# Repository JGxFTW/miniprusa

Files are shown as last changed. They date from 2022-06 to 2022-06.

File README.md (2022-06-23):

# miniprusa MC3 
## FDM/FFF 3D printer project

Heavy Duty, small factor, cartesian (bedslinger) machine capable of printing high detail plastic prints (PLA, PETG, TPU and possibly ABS, ASA, other high-temp materials). Project is loosely based on Bearmod project for Prusa i3. Utilizes out-of-the-shelf components and 3d prints.

Fusion360 model: https://a360.co/3Ne5RhL

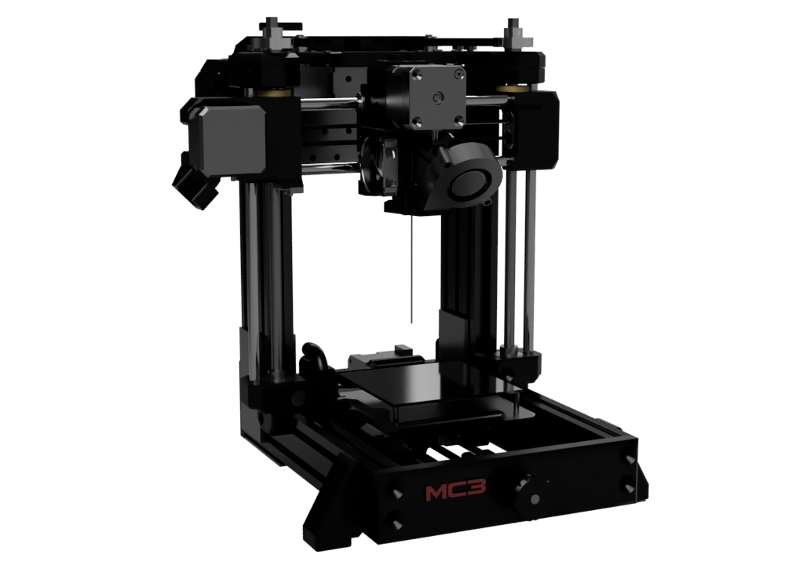
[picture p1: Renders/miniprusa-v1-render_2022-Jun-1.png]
miniprusa render


## Features

- ~100x100x110 [mm] build volume
- Direct MK3s extruder [remixed] for MK8/HobbGoblin drive gear and filament sensor (switch)
- Popular [Bearmod] XZ axis design, inverted
- LM8UU and 8mm smooth rods linear guide
- Rigid metal frame out of steel plates, 2040 and 2060 aluminum profiles
- Dual Z axis is driven independent with 1:2 gear ratio with nema 17 motor for each side
- [Marlin] 2.0.9.1 with auto bed leveling
- Custom ergonomic controller with OLED and encoder

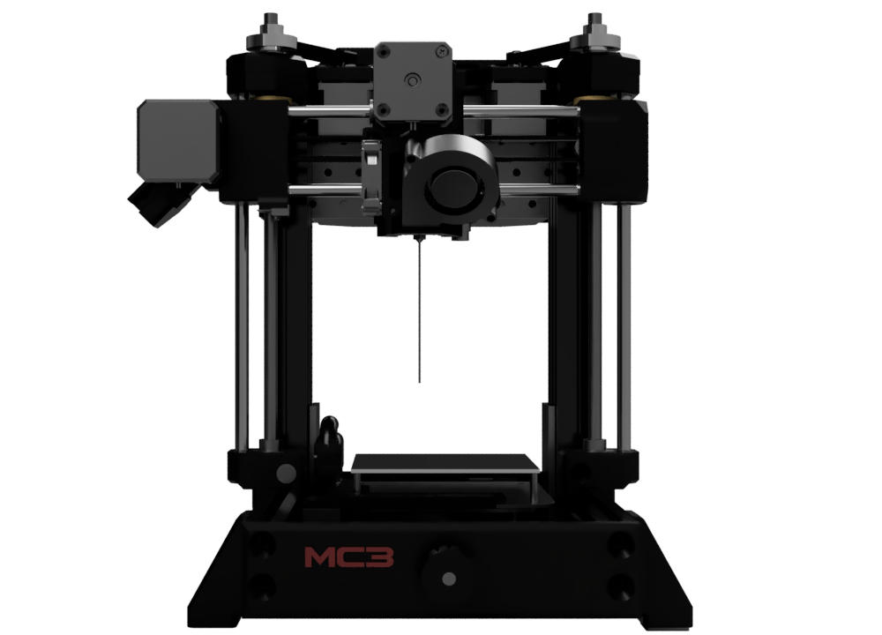
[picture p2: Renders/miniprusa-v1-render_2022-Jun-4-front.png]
miniprusa render

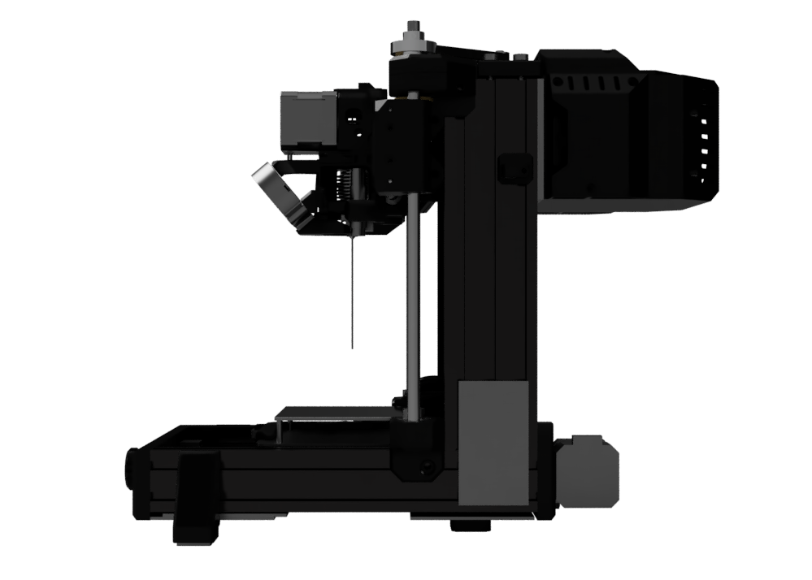
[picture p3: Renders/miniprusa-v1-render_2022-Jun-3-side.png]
miniprusa render

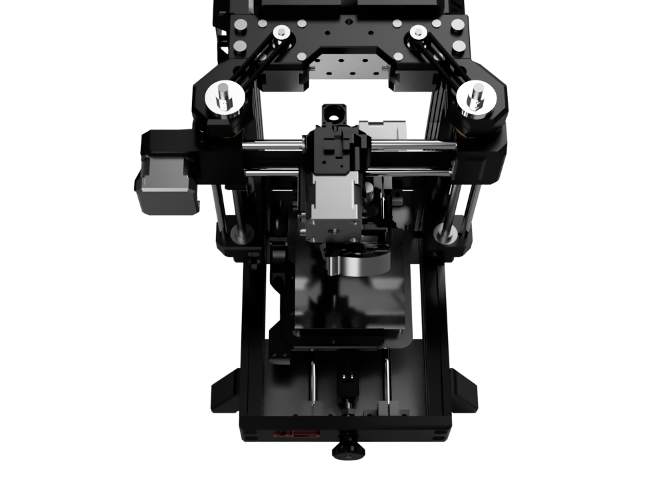
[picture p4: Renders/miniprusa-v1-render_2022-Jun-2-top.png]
miniprusa render

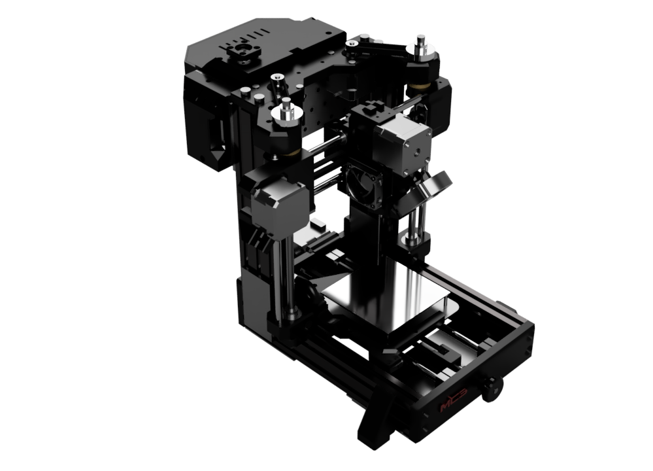
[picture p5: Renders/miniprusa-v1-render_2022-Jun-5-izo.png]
miniprusa render


## Technical details

### Frame
Frame consists of 2040 and 2060 aluminum extrusion profiles with 6mm groove. Steel plates and 3 printed bars (front, back and top) are holding extrusions in place secured with M5 screws and t-nuts.

### XYZ drive
Nema 17 stepper drivers for all axes. GT2 belt and pulleys. Dual Z axis consist of two trapezoidal screws with 8mm pitch (TR8x2) driven by independent motors with 1:2 gear ratio (GT2 T20 and GT2 T40).

### Extruder
Extruder is simplified PRUSA MK3 extruder with HobbGoblin/MK8 drive gear and 624ZZ idler bearing (PRUSA MK2s style).

Very consistent extrusion ;) 

### Electronics
Currently project uses RAMPS (https://reprap.org/wiki/RAMPS_1.4), as it is the most common mainboard.

Link to: [OLED Controller with encoder] project.

Power supply should be at least 200W
PSU is not mounted on the frame as printer was supposed to be in enclosure.

### Additions
Two types of cable tubing hoses 10mm (X,Y axes and OLED controller) and 16/17mm (extruder)

## BOM
The design require printed parts, so owning, renting 3d printer or outsourcing is needed.
Material PETG (open) or ABS, ASA (especially, if enclosing) are recommended.

Full [BOM spreadsheet] file.

Summary:
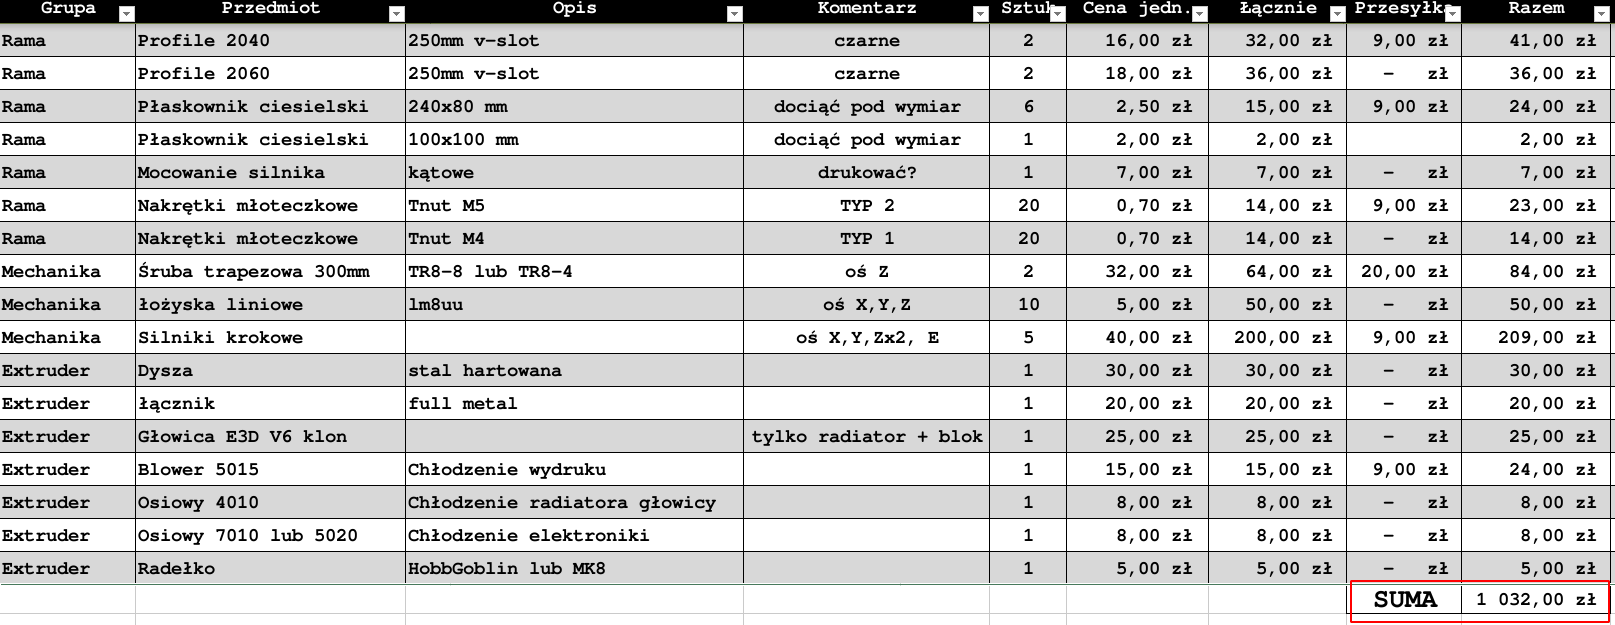
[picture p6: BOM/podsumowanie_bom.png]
BOM podsumowanie


## Firmware changes

Marlin 2.0.9.1 (v1.1) binary included - compiled for Ramps 1.4 and [miniOLED].

## Development

Want to contribute? Great!

To do:
> - revise Y axis
  - change endstop position
  - redesign bed plate
  - consider 
- redesign Z axis (one motor & synchronous belt drive)
> - BOM (translate, ensure correct number of screws and bolts, update links, double-check content)
 
Feel free to leave additional feedback.

[Forum thread] in Polish

## License

GPLv3

**Open Source, Hell Yeah!**

[//]: # (REFLINKS)
   [bearmod]: <https://www.thingiverse.com/thing:4362586>
   [remixed]: <https://www.thingiverse.com/thing:4566108>
   [Marlin]: <https://marlinfw.org/>
   [BOM spreadsheet]: <https://github.com/jgxftw/miniprusa/BOM/>
   [Reprap Forum thread]:<https://reprap.org/forum/read.php?13,499572,page=1>
   [Forum thread]: <https://reprapy.pl/viewtopic.php?f=78&t=7788&hilit=ma%C5%82a+czarna#p127598>
   [OLED Controller with encoder]: <https://github.com/jgxftw/minioled>
   [miniOLED]: <https://github.com/jgxftw/minioled>

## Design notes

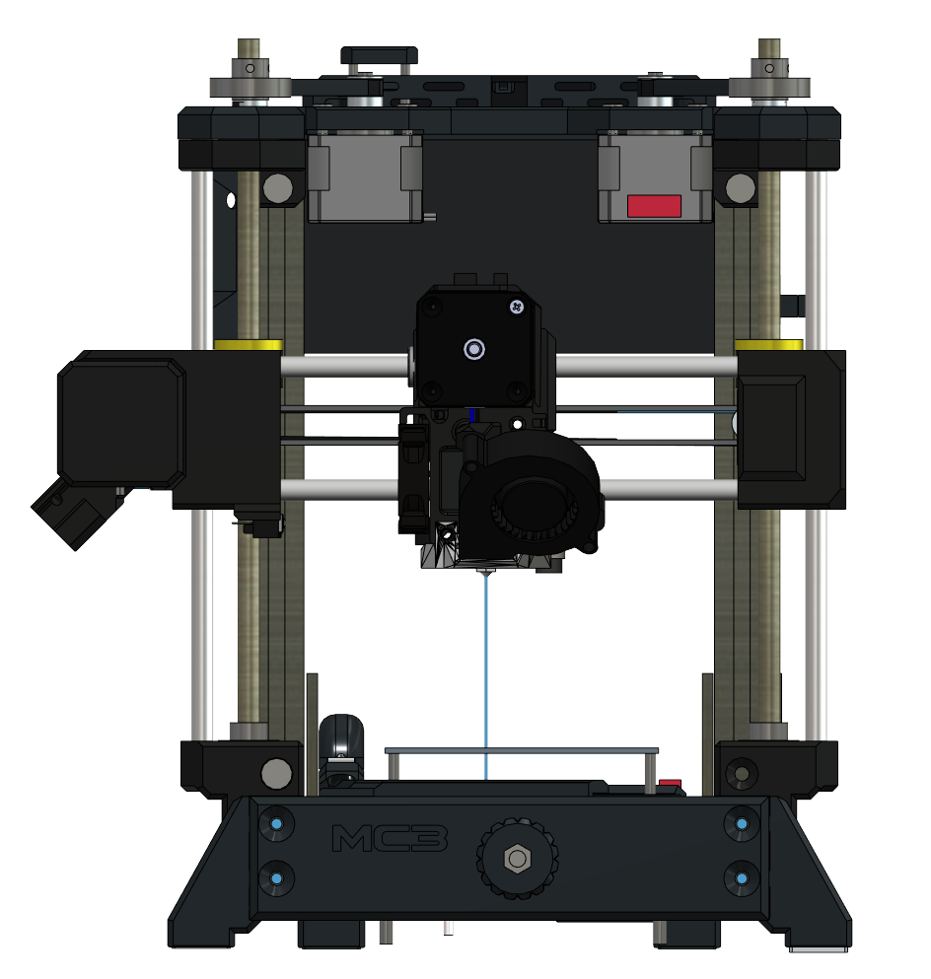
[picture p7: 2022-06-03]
Renders/miniprusa-all-v1-front.png

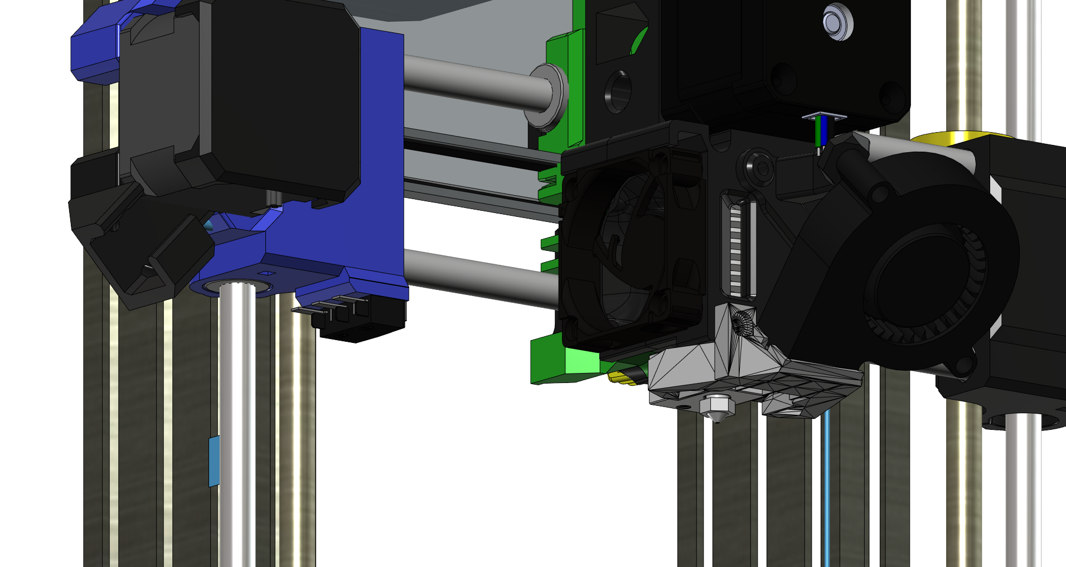
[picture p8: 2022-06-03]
Renders/endstop.png

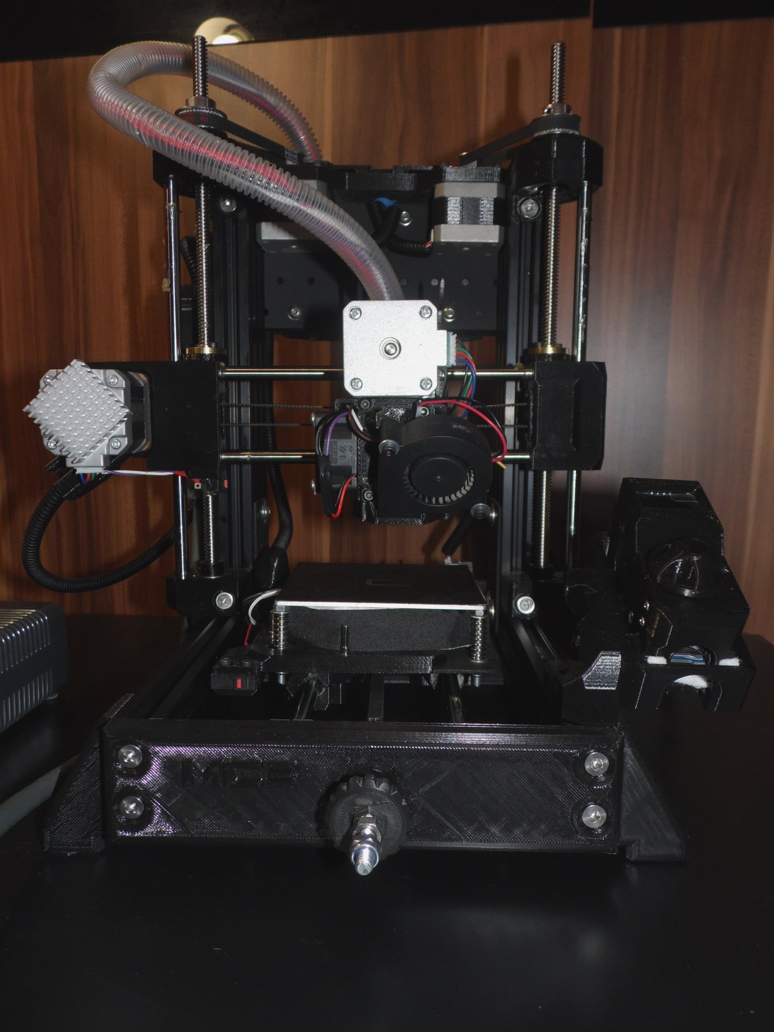
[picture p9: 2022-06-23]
Pictures/1-front3.JPG

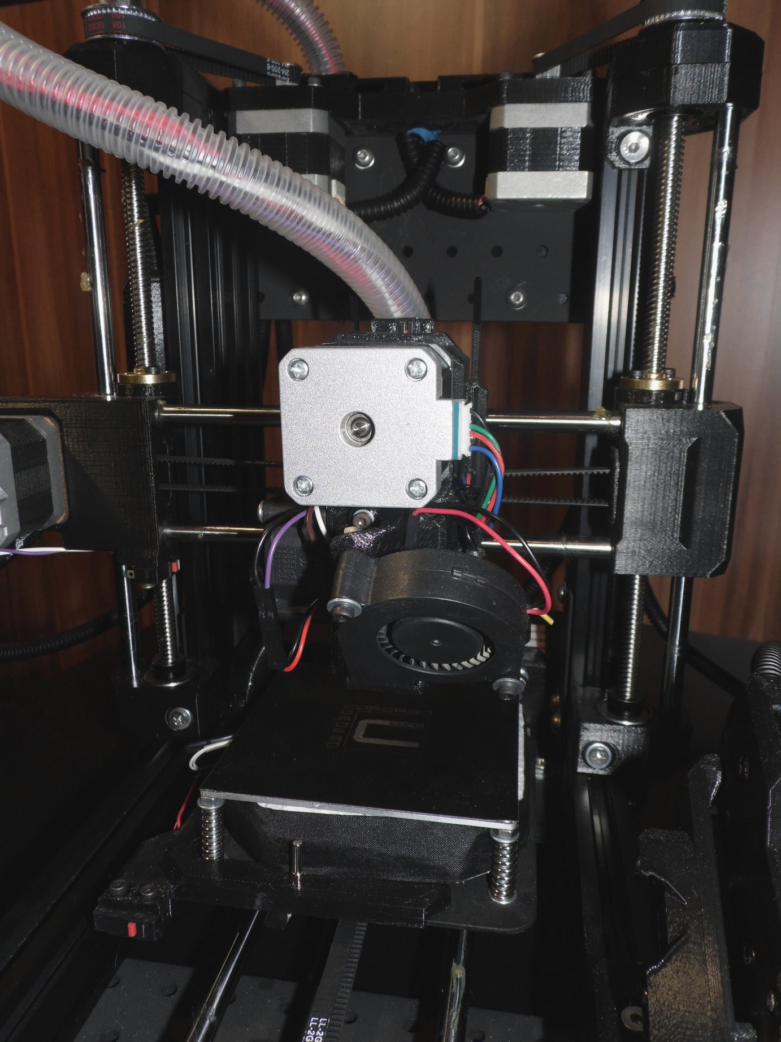
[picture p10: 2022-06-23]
Pictures/1-front2.JPG

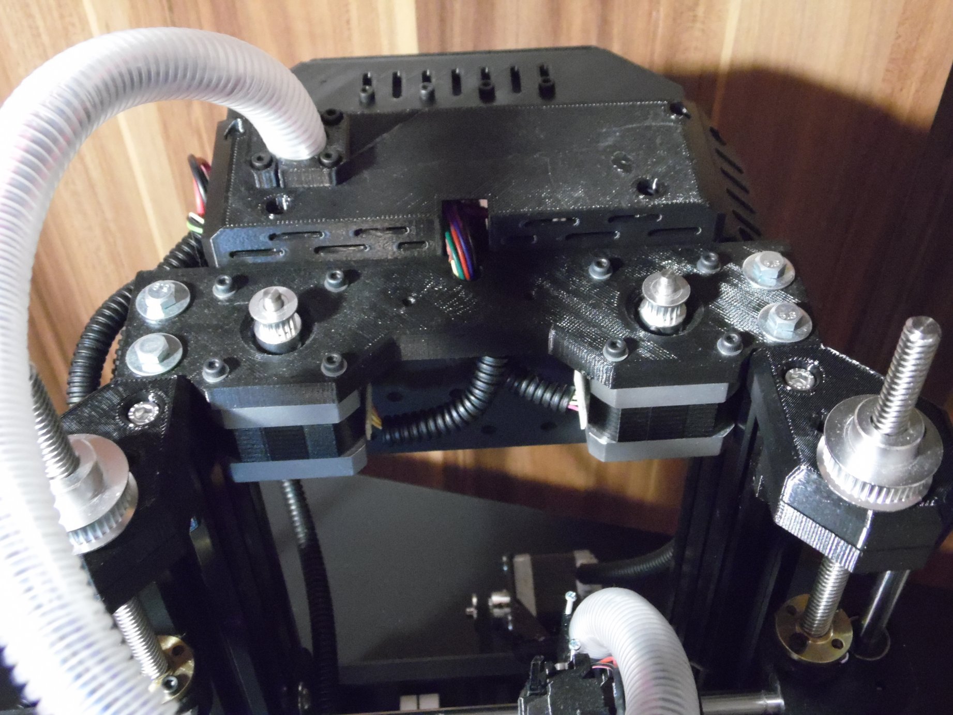
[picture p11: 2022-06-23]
Pictures/gora.JPG

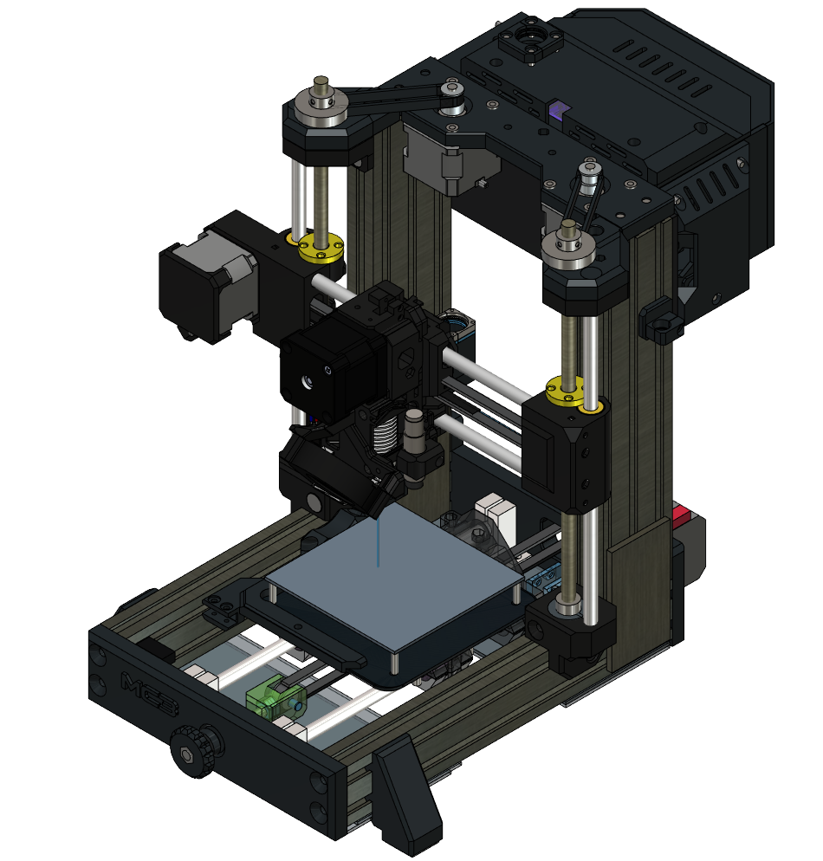
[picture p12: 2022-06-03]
Renders/miniprusa-all-v1-izo.png

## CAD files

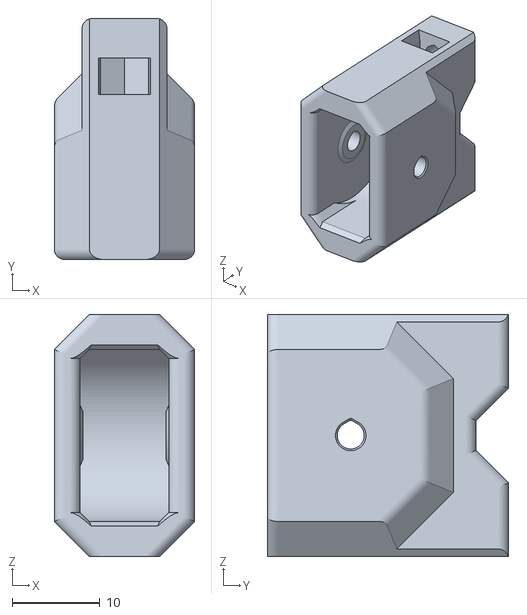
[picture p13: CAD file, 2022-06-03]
STL/Extruder/x-axis-idler-housing.stl
16.0 x 27.5 x 27.6

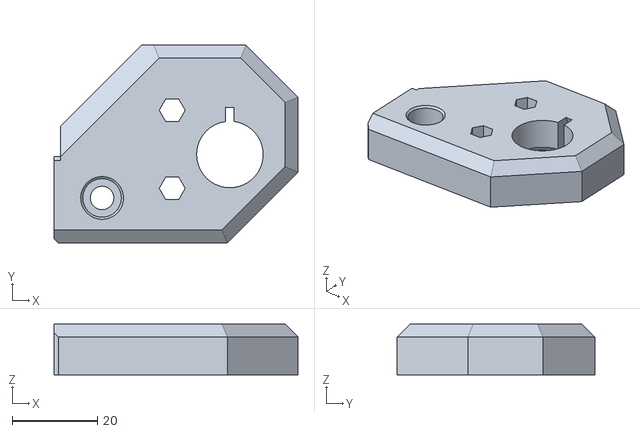
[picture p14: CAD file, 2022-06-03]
STL/z-axis-upper-cover-right.stl
57.1 x 46.2 x 11.9

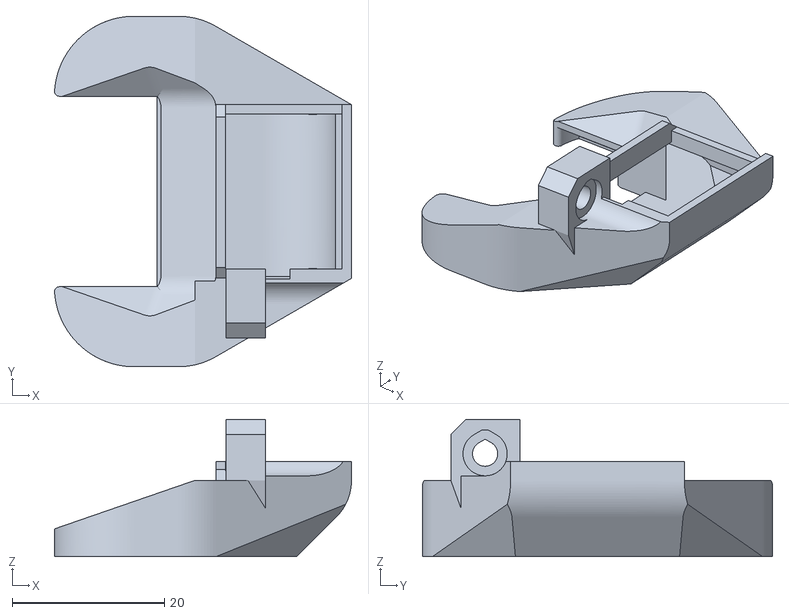
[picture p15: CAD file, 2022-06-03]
STL/Extruder/fan_duct_mk3_bearmod.stl
39.0 x 46.0 x 18.0

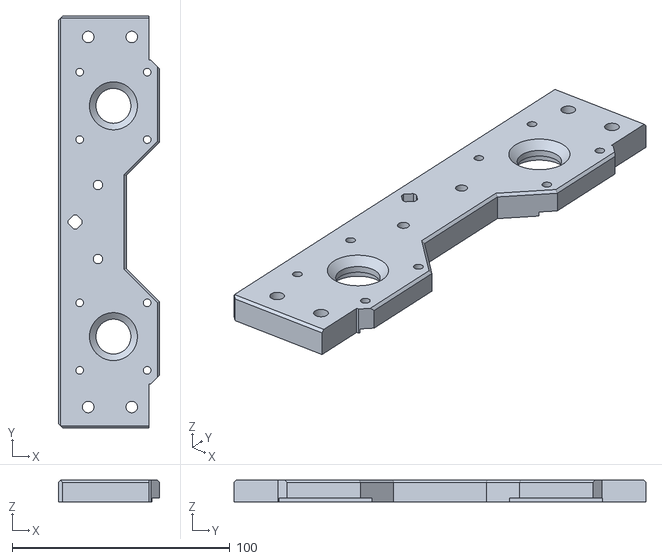
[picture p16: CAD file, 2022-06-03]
STL/z-axis-upper-reinforcementv_0_9.stl
46.6 x 189.2 x 10.0

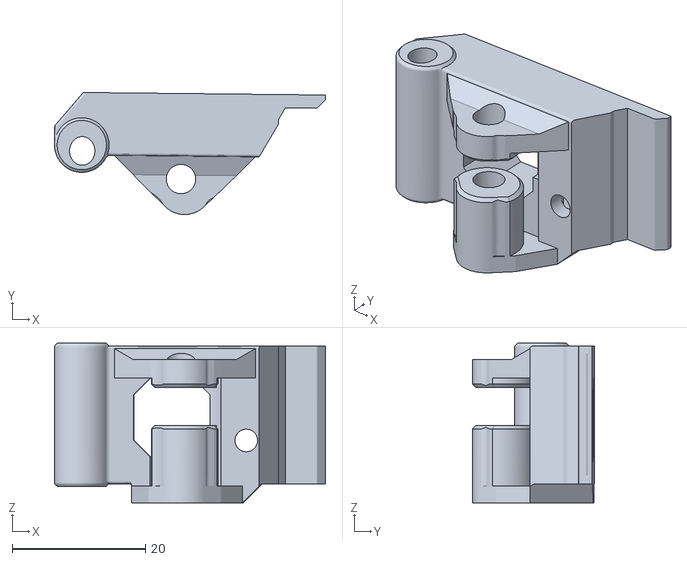
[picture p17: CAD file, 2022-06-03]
STL/Extruder/idler_v2.stl
40.7 x 18.3 x 23.9

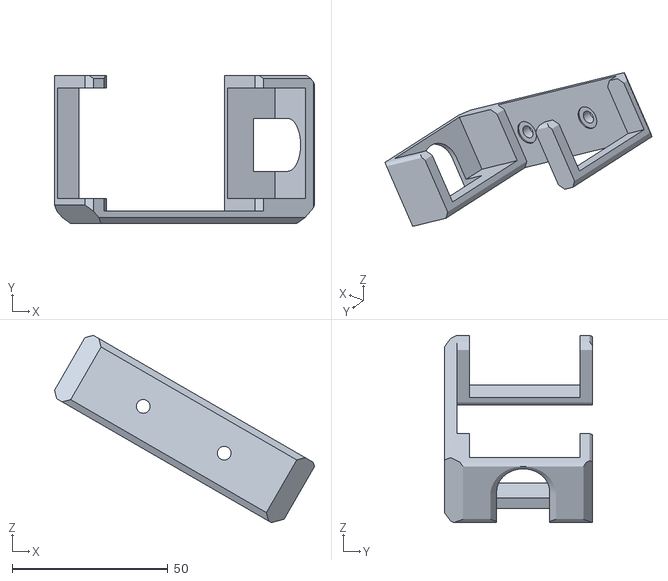
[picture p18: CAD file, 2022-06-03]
STL/lcd-screen-frame-mount-base.stl
83.4 x 47.6 x 60.1

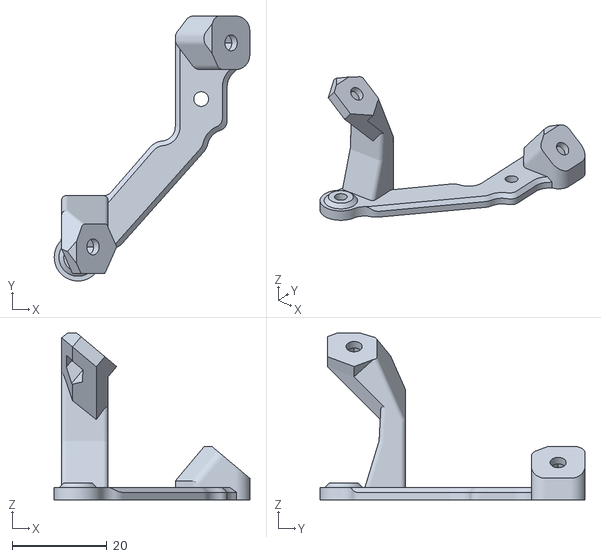
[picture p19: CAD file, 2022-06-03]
STL/Extruder/MK3_Extruder_fan_mount.stl
41.2 x 55.8 x 35.2

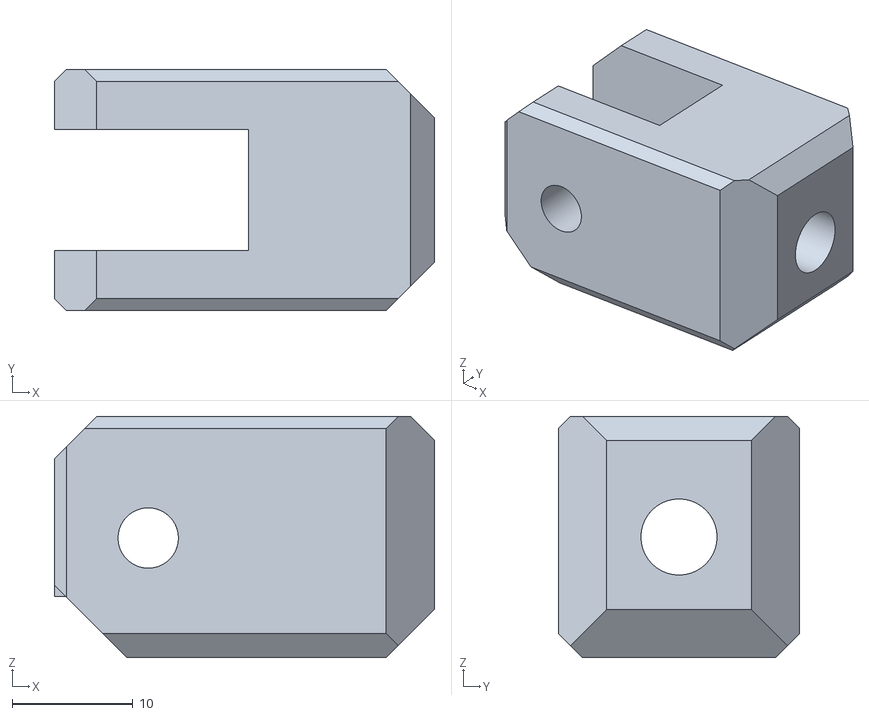
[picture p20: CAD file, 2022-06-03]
STL/y-axis-belt-tensioner-v3.stl
31.5 x 20.0 x 20.0

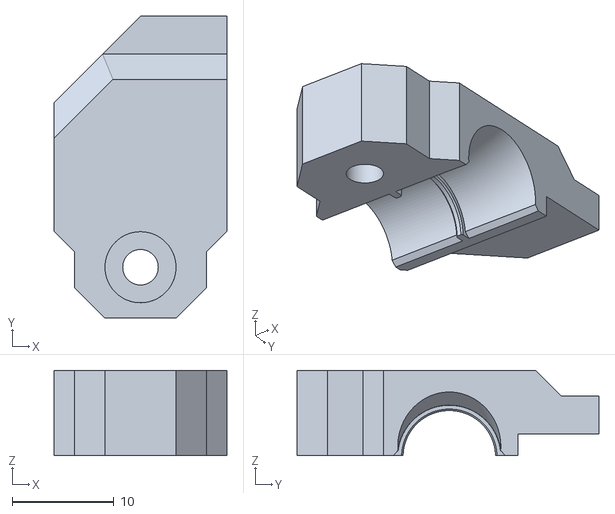
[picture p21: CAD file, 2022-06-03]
STL/bed-cable-chain-mount-clamp.stl
17.0 x 29.7 x 8.38

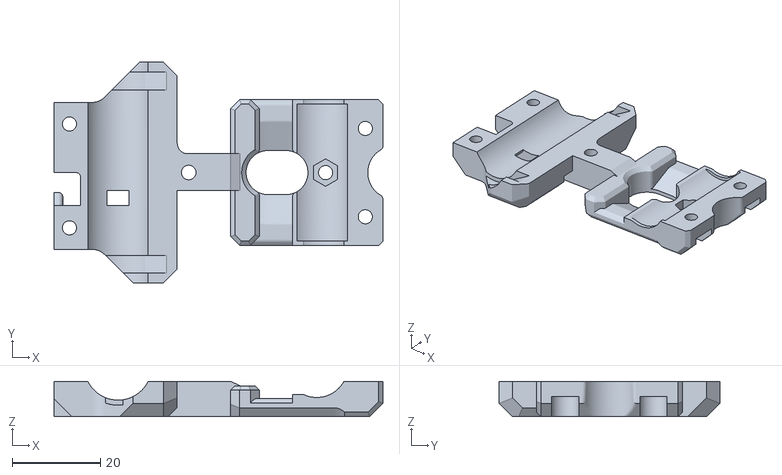
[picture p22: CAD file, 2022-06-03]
STL/Extruder/MK3_Extruder_x_carriage_cover.stl
74.5 x 50.0 x 8.00

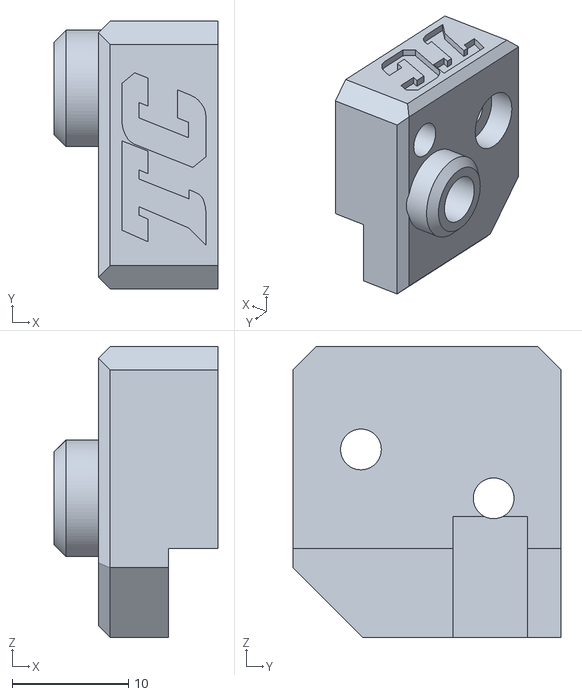
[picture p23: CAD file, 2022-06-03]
STL/Extruder/MK3_Extruder_rewizja_filament_sensor_cover.stl
14.1 x 23.0 x 25.0

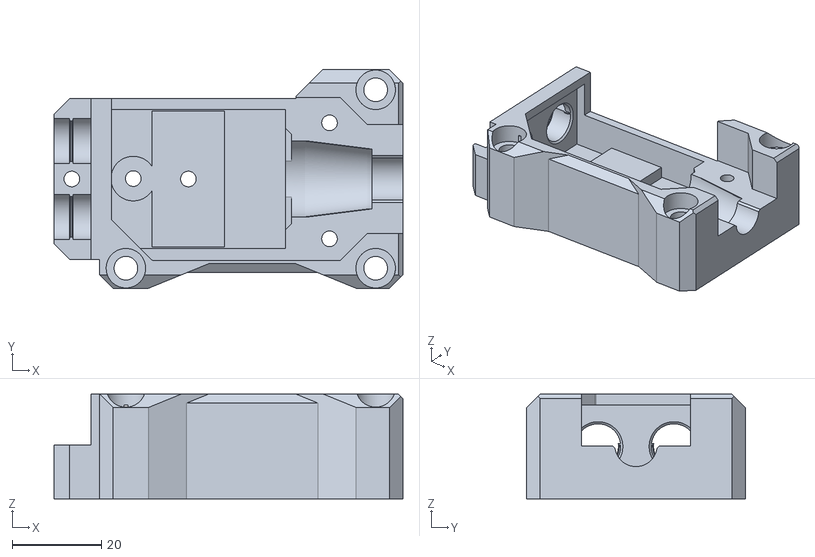
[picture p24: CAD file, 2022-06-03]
STL/xbox360-psu-power-inlet-base.stl
78.2 x 49.0 x 23.5

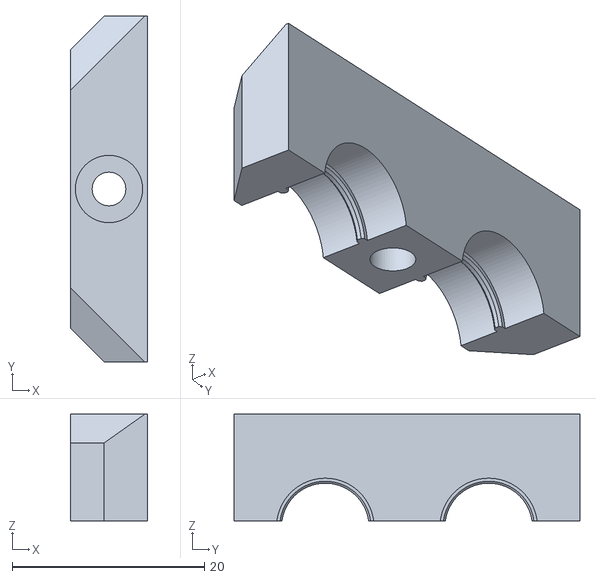
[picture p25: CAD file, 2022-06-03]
STL/xbox360-psu-power-inlet-clamp.stl
8.00 x 36.0 x 11.1

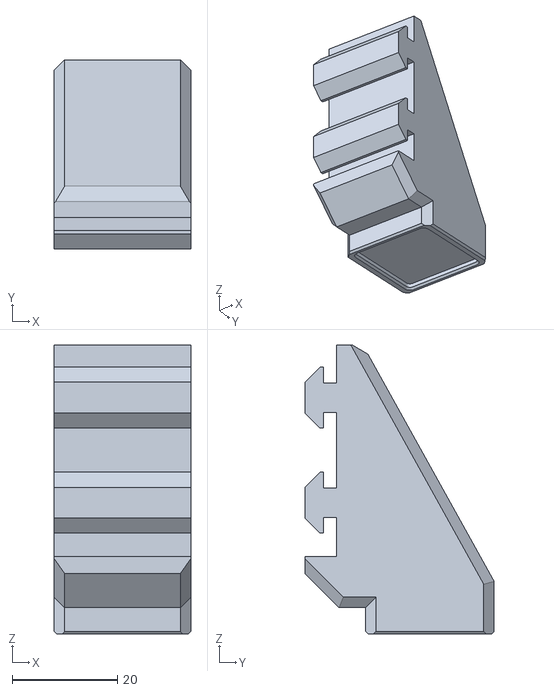
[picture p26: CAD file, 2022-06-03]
STL/base-legs.stl
26.0 x 36.1 x 55.0

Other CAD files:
STL/Extruder/MK3_Extruder_rewizja_idler.stl
STL/electronics-box-upper-cover-addon.stl
STL/z-axis-lower-trapezoidal-mount.stl
STL/LCD-screen-cable-mount.stl
STL/base-legs-v2.stl
STL/base-rear-legs.stl
STL/bed-cable-chain-mount-clamp-v2.stl
STL/bed-cable-chain-mount-clamp-v3.stl
STL/bed-cable-chain-mount-clamp-v4.stl
STL/bed-cable-chain-mount-clamp-v5stl.stl
STL/electronics-box-base-addon.stl
STL/electronics-box-base-v2.stl
STL/electronics-box-base.stl
STL/electronics-box-front-cover-B.stl
STL/electronics-box-side-covers--v2.stl
STL/electronics-box-side-covers-left-v3.stl
STL/electronics-box-upper-cover-base.stl
STL/electronics-box-upper-cover-cable-chain-holder.stl
STL/electronics-box-upper-cover-lid.stl
STL/extruder-cable-chain-base.stl
STL/extruder-cable-chain-clamps.stl
STL/extruder-nozzle-fan-duct.stl
STL/extruder-print-cooling-fan-mount.stl
STL/lcd-screen-frame-mount-rest.stl
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

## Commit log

2022-06-08 Firmware v1.1 for miniprusa MC3
    Marlin 2.0.9.1 binary file for Ramps 1.4 and miniOLED
2022-06-23 new renders
    updated renders of CAD model - 06/22
2022-06-23 new renders
    updated render of CAD model - 06/22
2022-06-24 Current slicing profiles and 3d model to import
    Slicing profiels for Simplify3D and 3d model to import into slicer
